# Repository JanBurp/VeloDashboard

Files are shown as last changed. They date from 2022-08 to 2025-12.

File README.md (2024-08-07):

# Velo Dashboard

A bicycle computer made for velomobiles.

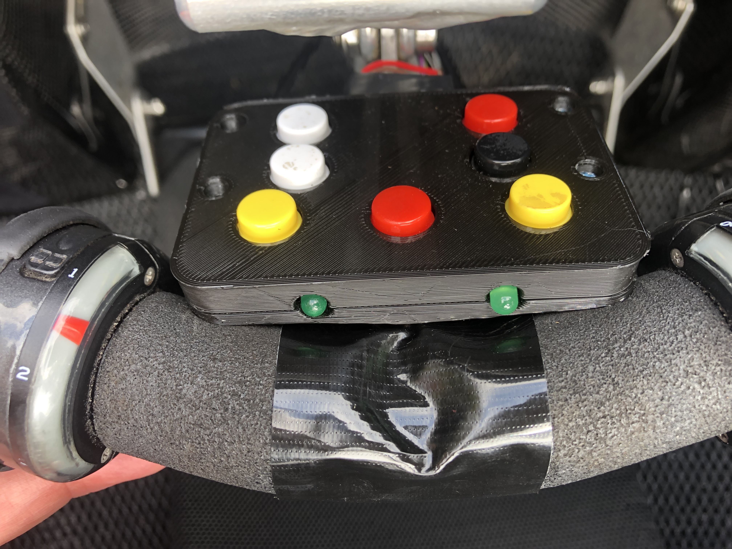
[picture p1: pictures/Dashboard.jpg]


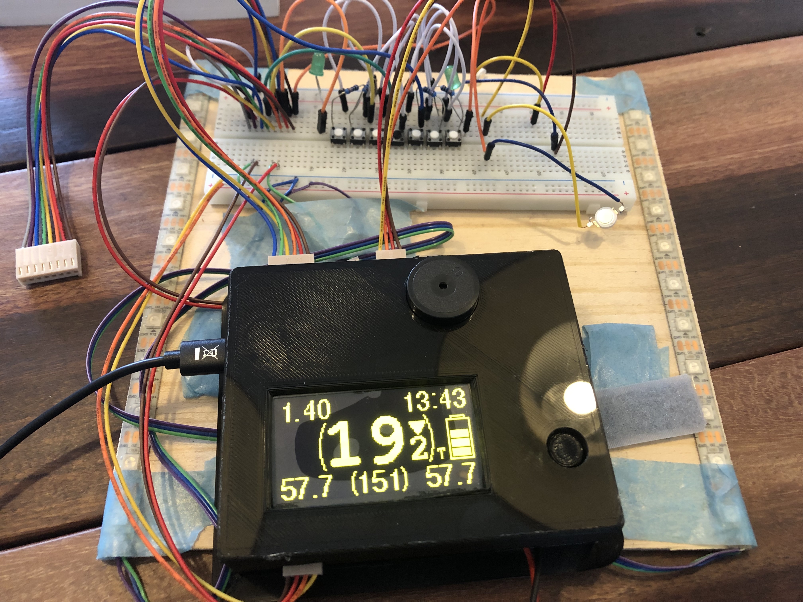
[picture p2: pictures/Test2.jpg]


Walkthrough videos (dutch):
- https://www.youtube.com/watch?v=hqzajXb8Hd0 (inside velomobile)
- https://www.youtube.com/watch?v=B8IcSTC7h3M (test setup)

## Reasons

In the summer of 2022 i bought a second hand [Quest](https://www.velomobiel.nl/quest/) velomobile.
It was in very good shape, had only driven 8000km while only 10 years old, and it fits my budget.

But it was missing blinkers, had a 6V system on board, and two headlights which could be turned on independent from eachother. Which results in my Quest looking cross-eyed :-(
That could be done better.

I also struggled finding the 'perfect' bicycle computer to keep track of at least my current speed, average speed, maximum speed, time, time of the trip, distance, and at least two seperate distance counters.
The most anoying things of these computers are the small screens, the not so ideal combination of functions, button combo's etc. And a GPS one took too long to recognise my location (possibly due to the carbon body).

I took some inspiration found online from other velonauts. Such as:
- [VeloPuter](https://veloputer.wordpress.com/about/)
- [Arduino in VM](https://quest.robbroek.nl/search/label/arduino)
- [Velomobiel Led strip verlichting](https://bickyenzijnfietsen.blogspot.com/2018/10/velomobiel-led-strip-verlichting.html)

## Features

This bicycle computer for a velomibile has these features:

Lighting:
- Drive the normal LED lights that are standard in most velombiles (rear light, brake light, fog light and blinkers if present)
- Drive the (double) head light(s) in several steps (off, dim, normal, beam)
- Drive LED strips on each side of the velomobile. For blinkers (with nice animation!), and normal light for visibility (front, rear and brake lights).

Knobs & Display:
- Big OLED display so i can see it easy.
- All controls are on the steering wheel (with a 3D printed console).
- Knobs for the blinkers, lights and switching through several pages on the display.

Speed & Distance:
- Current speed
- Current average speed
- Current maximum speed
- Distance of current trip
- Total distance of current day
- Distance of previous day
- Average and maximum speed of previous day
- Total distance of the velomobile in total
- Total distance of the velomobile while in my ownership
- At least three different tocal counters wich can be reset independent

Time:
- Current clock time
- Driving time of current trip (excluding stops for traffic lights etc)
- Total time of current trip (including these stops)
- Driving and total time of previous day

Others:
- Current Cadans speed
- Battery status
- Battery saving modes
- Automatic turn off after a set time (to spare battery)
- Option to set the total distance
- Option to set the clock time
- Option to set the wheel circumference
- Optionts to reset all extra counters

# Result

I have a working prototype since december 2022, with several improvements and new featuers since then.

# Manual

## Dashboard



- The yellow buttons are for activating the blinkers. Press and it turns on. Press again to turn off. Press the other and the first one stops and the new one starts. The LED's in front of the dashboard reflects the state of the blinkers.
- The white buttons are for controlling the head and rear lights. And also the lights of the LEDstrips. Press the upper button increases intensity. The lower button decreases intensity. These modes exists: OFF, DIMLIGHT, NORMAL LIGHT, BEAM, FOG.
- The red button on the upper right turns the headlights into BEAM mode while pressed.
- The red button in the middle is not part of the computer: it is it's own circuit and turns of the horn (in my case a Hornitt).
- The black button on the right is for controlling the display on the computer. Pressing cycles to several pages of the display (see below). Long press turns the computer and display into SETUP mode (see below).

## Display modes

Normal pages of the display (cycles through with the blank button):

### Homescreen:
- Speed (big in the center)
- Current distance (topleft)
- Current clock time (topright)
- Average speed (bottomleft)
- Maximun speed (bottomright)
- Cadans / RPM (bottomcenter)
- Icons for headlights and rearligt (middleleft)
- Icons for blinkers and breaklight (topmiddle)
- Icon for battery status (middleright)

### Screen 2 (today):
- Average speed
- Max speed
- Time elapsed while driving (excluding stops)
- Time elapsed from start of driving (including stops)

### Screen 3 (distances):
- Distance of current drive
- Distance of today
- Distance of previous driving day
- Distance of Trip 1

### Screen 3 (totals):
- Total distance of velomobile in my ownershop
- Total distance of velomobile
- Distance of Trip 2
- Distance of Trip 3

## Setup

A long press on the blank button switches to the setup screens. And pressing normal cycles to the setup screens. Long pressing again switches to normal screens. Of the screens there is some help of how to setup the several options.

These are the setup pages:

- Trip - for resetting Trip 1,2 and 3.
- Clock - for setting the time
- Tyre -  for setting the tyre (used for measuring speed and distances). You can select and ERTRO value or in mm.
- Bike - setting the total distance of the bike.

## Others

The computer keeps track of battery status. If the battery is becoming low it will decreases the brightness of the LEDstrips the battery icon on the display starts to blink.

If the battery is very low/almost dead, it will spare itself by turning everything off.

If you forgot to switch the computer off, if will auto power off after three minutes. The last 20 seconds will be shown in the display. If you press a button or start cycling again, the auto-power-off timer will stop.

## Hardware

### Teensy 4.0

The computer is based around a [Teensy 4.0](https://www.pjrc.com/store/teensy40.html). My first attempt was made with a Arduino nano, which is cheaper and uses less power. But i wanted a clock. And the combination of driving LED strips and having an OLED screen was impossible (as far as i know) with te Arduino. The Teensy 4.0 has multiple i2c (OLED) and interrupts. And it also has a build in RTC (Real Time Clock) with power options for a small coin battery to keep the state of the clock. The Teensy has also lots of room for improvements or future additions (SD card storage for example).

### IP67 LEDstrips WS2812B

IP67 means rainproof. And WS2812B means it just has three wires to connect (5V, GND & Data). I have two of them, one for each side of the velomobile. But the computer can also run four of them in case you want four small ones instead of two large ones. I choose the large ones because of easier assembling on my Quest. Downside is it user more power.
Here is a guide for using [WS2812B LEDstrips](https://randomnerdtutorials.com/guide-for-ws2812b-addressable-rgb-led-strip-with-arduino/)

### Power

- For power i choose Lipo batteries of 12.6 Volts. Other batteries are possible.
- [Polo Mini Pushbutton Power Switch](https://www.pololu.com/product/2809) is a on/off switch, whith reverse protection and more.
- Power regulator to 5V. The Teensy has it's own regulator for 5V to 3.3V.

### LED drivers

For driving the front, rear, brake (and maybe blinker) LED's i use [Meanwell LDD Led drivers](https://www.meanwell.com/webapp/product/search.aspx?prod=LDD-L) (LDD-700 for now).

## Schematics

The raw schematics can be found in the [kicad folder](./kicad)

## Software

For developing i used [VScode](https://code.visualstudio.com/) with [PlatformIO](https://platformio.org/). Once setup, i found this much easier for developling compared the Arduino IDE. But thats a software developer speaking ;-)

## 3D print

A STL file for 3D printing the console can be found in the [3D folder](./3d).

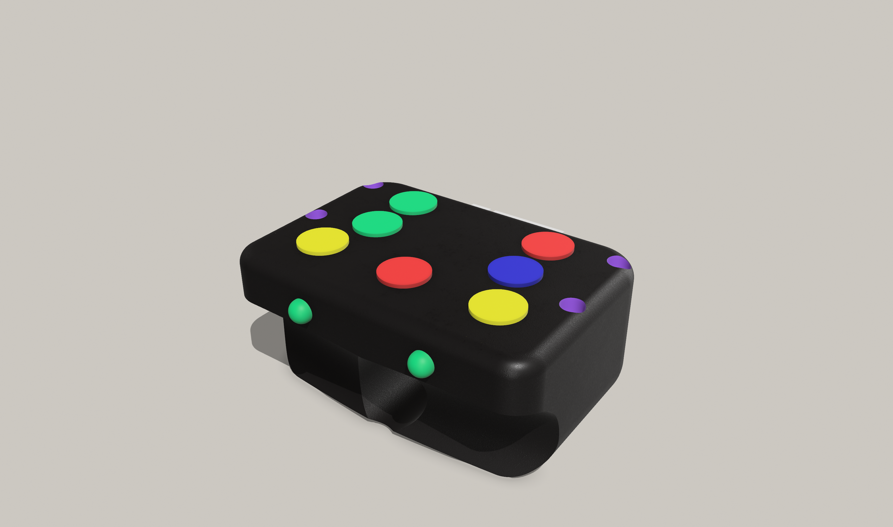
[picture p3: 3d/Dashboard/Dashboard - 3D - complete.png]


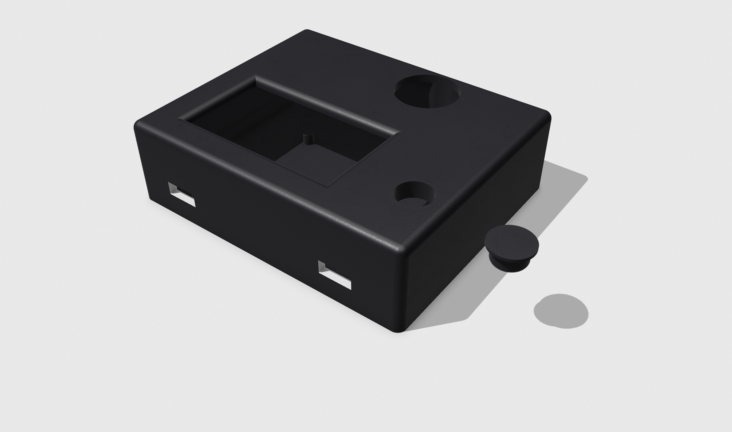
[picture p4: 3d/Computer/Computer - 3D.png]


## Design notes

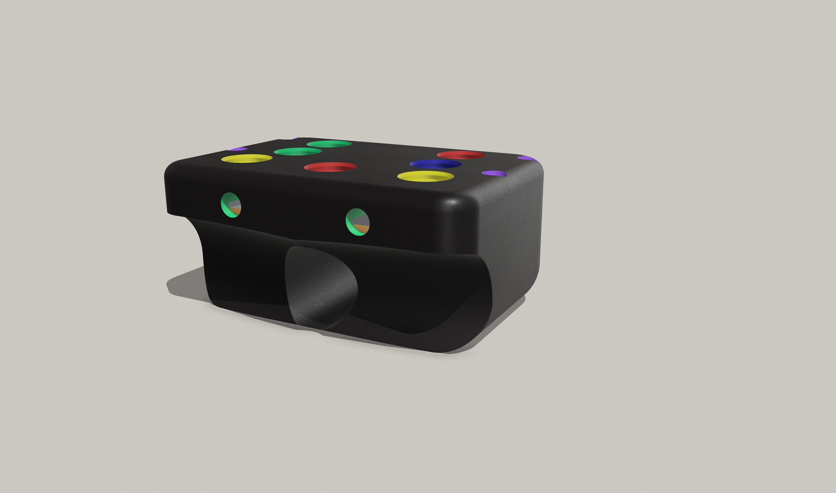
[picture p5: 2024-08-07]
3d/Dashboard/Dashboard_3D.png

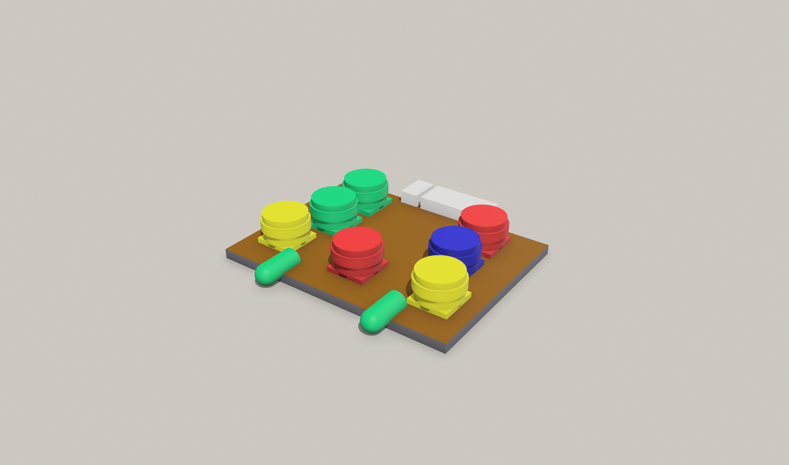
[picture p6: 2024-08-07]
3d/Dashboard/PCB-3D-sketch.png

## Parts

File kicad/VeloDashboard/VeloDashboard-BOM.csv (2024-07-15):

Reference | Value | Datasheet | Footprint | Qty | DNP
BT1 | Battery Cell 3.3V | ~ | Battery:Battery_Panasonic_CR2032-HFN_Horizontal_CircularHoles | 1
C1 | 22µF | ~ | Capacitor_THT:CP_Radial_D10.0mm_P7.50mm | 1
D1 | LEFT | ~ | LED_THT:LED_D5.0mm_Clear | 1
D2 | RIGHT | ~ | LED_THT:LED_D5.0mm_Clear | 1
IC1,IC2,IC3,IC4,IC5,IC6 | LDD-700L | https://datasheet.datasheetarchive.com/originals/distributors/DKDS-14/277848.pdf | LDD:LDD-XXXL | 6
J1 | OLED | ~ | Connector_PinHeader_2.54mm:PinHeader_1x04_P2.54mm_Horizontal | 1
J1.in1 | ~ | ~ | Connector_PinHeader_2.54mm:PinHeader_1x07_P2.54mm_Horizontal | 1
J1.out1 | Polulu Power | ~ | Connector_PinHeader_2.54mm:PinHeader_1x06_P2.54mm_Horizontal | 1
J2 | LED STRIPS | ~ | Connector_PinHeader_2.54mm:PinHeader_1x04_P2.54mm_Horizontal | 1
J3 | To Dashboard | ~ | Connector_PinHeader_2.54mm:PinHeader_1x08_P2.54mm_Horizontal | 1
J4 | To Computer | ~ | Connector_PinHeader_2.54mm:PinHeader_1x08_P2.54mm_Horizontal | 1
J5 | Speed Sensor | ~ | Connector_PinHeader_2.54mm:PinHeader_1x03_P2.54mm_Horizontal | 1
J6 | Headlights | ~ | Connector_PinHeader_2.54mm:PinHeader_1x04_P2.54mm_Horizontal | 1
J7 | Rearlights | ~ | Connector_PinHeader_2.54mm:PinHeader_1x04_P2.54mm_Horizontal | 1
J8 | Blinkers | ~ | Connector_PinHeader_2.54mm:PinHeader_1x04_P2.54mm_Horizontal | 1
J9 | PowerSwitch | ~ | Connector_PinHeader_2.54mm:PinHeader_1x02_P2.54mm_Horizontal | 1
J10 | Addon 1 | ~ | Connector_PinHeader_2.54mm:PinHeader_1x03_P2.54mm_Horizontal | 1
J11 | Addon 2 | ~ | Connector_PinHeader_2.54mm:PinHeader_1x03_P2.54mm_Horizontal | 1
J12 | extra led strips | ~ | Connector_PinHeader_2.54mm:PinHeader_1x04_P2.54mm_Horizontal | 1
R1 | 4M | ~ | Resistor_THT:R_Axial_DIN0207_L6.3mm_D2.5mm_P10.16mm_Horizontal | 1
R2 | 1M | ~ | Resistor_THT:R_Axial_DIN0207_L6.3mm_D2.5mm_P10.16mm_Horizontal | 1
R3,R4,R5,R11,R12,R17,R18 | 100k | ~ | Resistor_THT:R_Axial_DIN0207_L6.3mm_D2.5mm_P10.16mm_Horizontal | 7
R6,R7,R8 | 220k | ~ | Resistor_THT:R_Axial_DIN0207_L6.3mm_D2.5mm_P10.16mm_Horizontal | 3
R9,R10 | 220 | ~ | Resistor_THT:R_Axial_DIN0207_L6.3mm_D2.5mm_P10.16mm_Horizontal | 2
R13,R14,R15,R16,R19,R20 | 47k | ~ | Resistor_THT:R_Axial_DIN0207_L6.3mm_D2.5mm_P10.16mm_Horizontal | 6
R21,R22,R23,R24 | 370 | ~ | Resistor_THT:R_Axial_DIN0207_L6.3mm_D2.5mm_P10.16mm_Horizontal | 4
SW2 | Left | ~ | Button_Switch_THT:SW_PUSH-12mm | 1
SW3 | Down (lights) | ~ | Button_Switch_THT:SW_PUSH-12mm | 1
SW4 | Up (lights) | ~ | Button_Switch_THT:SW_PUSH-12mm | 1
SW5 | Brake | ~ | Button_Switch_THT:SW_PUSH-12mm | 1
SW6 | Horn | ~ | Button_Switch_THT:SW_PUSH-12mm | 1
SW7 | Display | ~ | Button_Switch_THT:SW_PUSH-12mm | 1
SW8 | Right | ~ | Button_Switch_THT:SW_PUSH-12mm | 1
U1 | SN74AHCT125N | http://www.ti.com/general/docs/suppproductinfo.tsp?distId=10 | Package_DIP:DIP-14_W7.62mm_Socket_LongPads | 1
U2 | LC78_05 2.0 | https://www.onsemi.cn/PowerSolutions/document/MC7800-D.PDF | Package_TO_SOT_THT:TO-220-3_Vertical | 1
U3 | Teensy4.0 |  | Teensy:Teensy40_SMT | 1

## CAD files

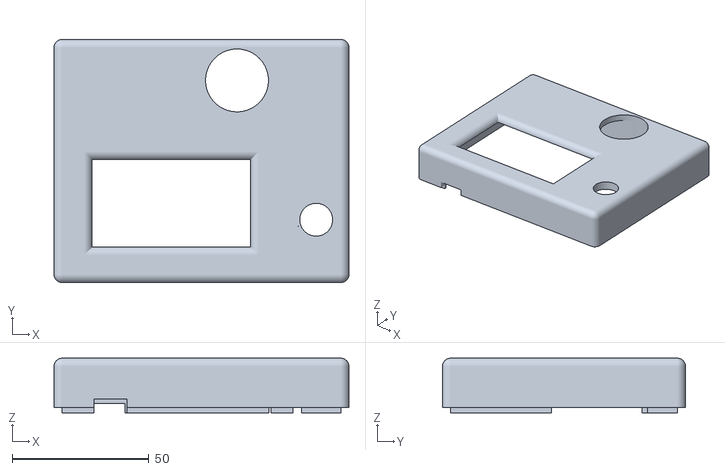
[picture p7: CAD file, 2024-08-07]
3d/Computer/Computer - top.stl
108.0 x 89.0 x 20.0

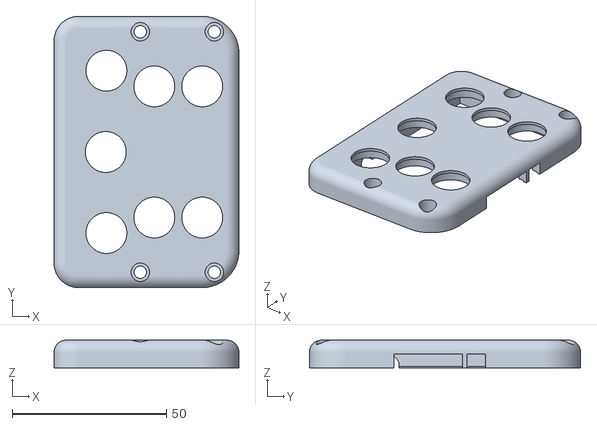
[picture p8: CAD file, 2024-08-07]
3d/Dashboard/VeloDashboard - v3 - top.stl
60.0 x 88.0 x 9.00

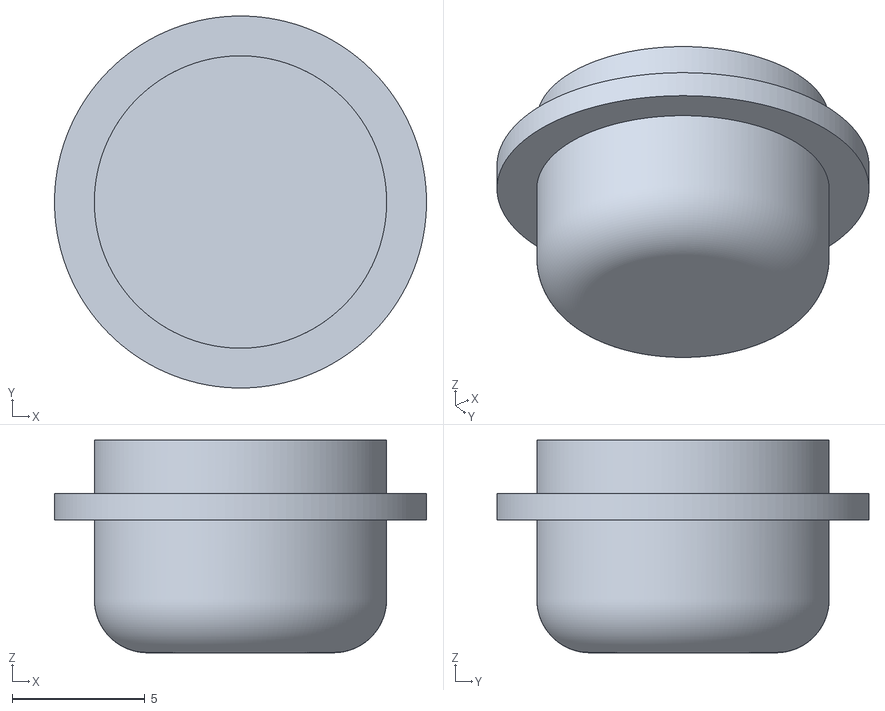
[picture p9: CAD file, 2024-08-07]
3d/Computer/Computer - button.stl
14.0 x 14.0 x 8.00

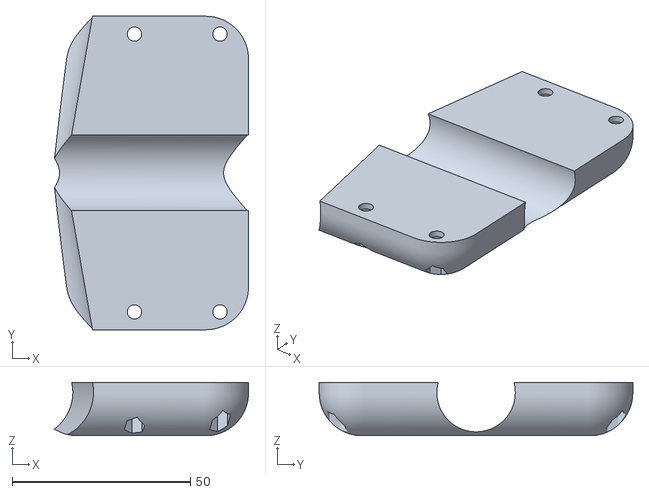
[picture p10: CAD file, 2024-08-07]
3d/Dashboard/VeloDashboard - v3 - bot.stl
54.4 x 88.0 x 15.0

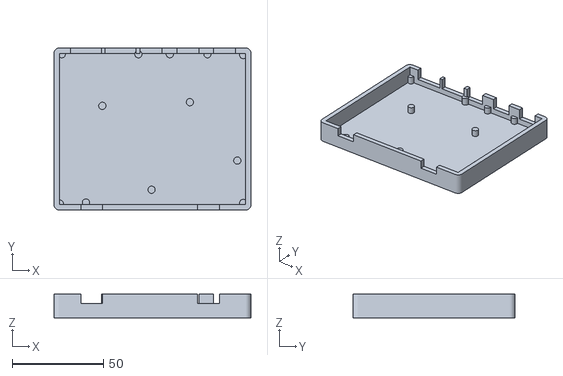
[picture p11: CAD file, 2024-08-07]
3d/Computer/Computer - bot.stl
108.0 x 89.0 x 13.0

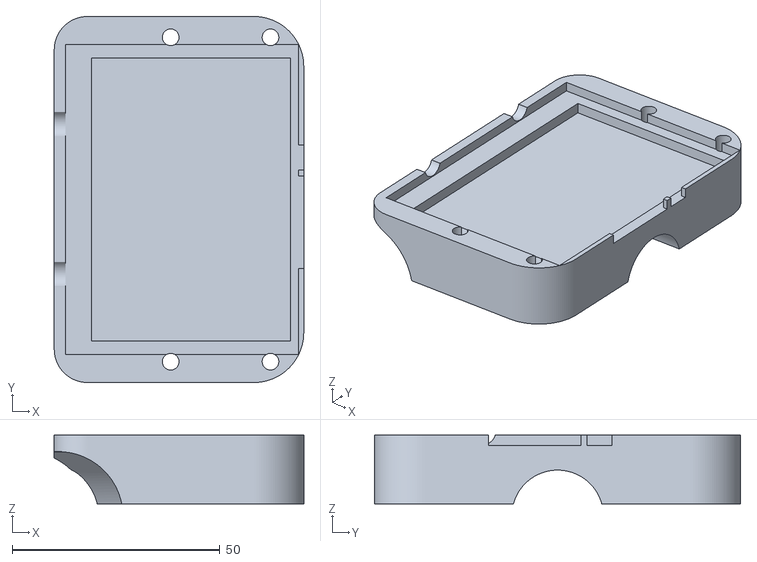
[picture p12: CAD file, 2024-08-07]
3d/Dashboard/VeloDashboard - v3 - mid.stl
60.0 x 88.0 x 16.5

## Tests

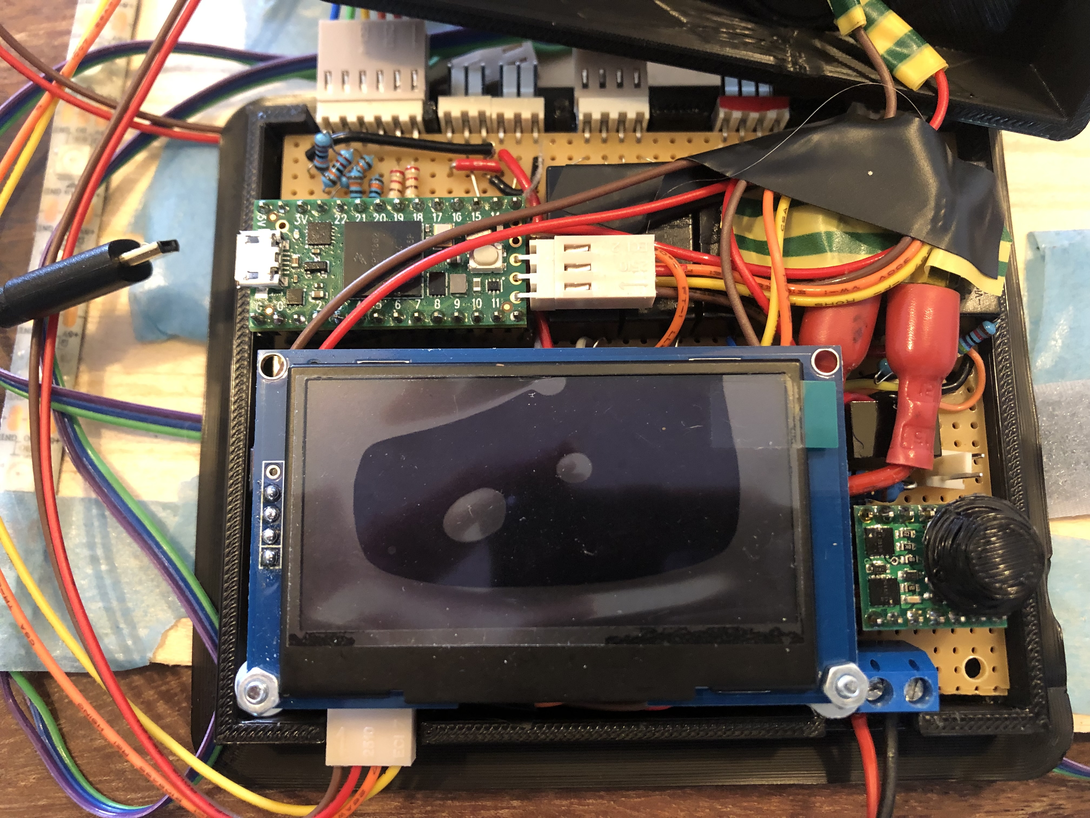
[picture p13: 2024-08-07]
pictures/Test1.jpg

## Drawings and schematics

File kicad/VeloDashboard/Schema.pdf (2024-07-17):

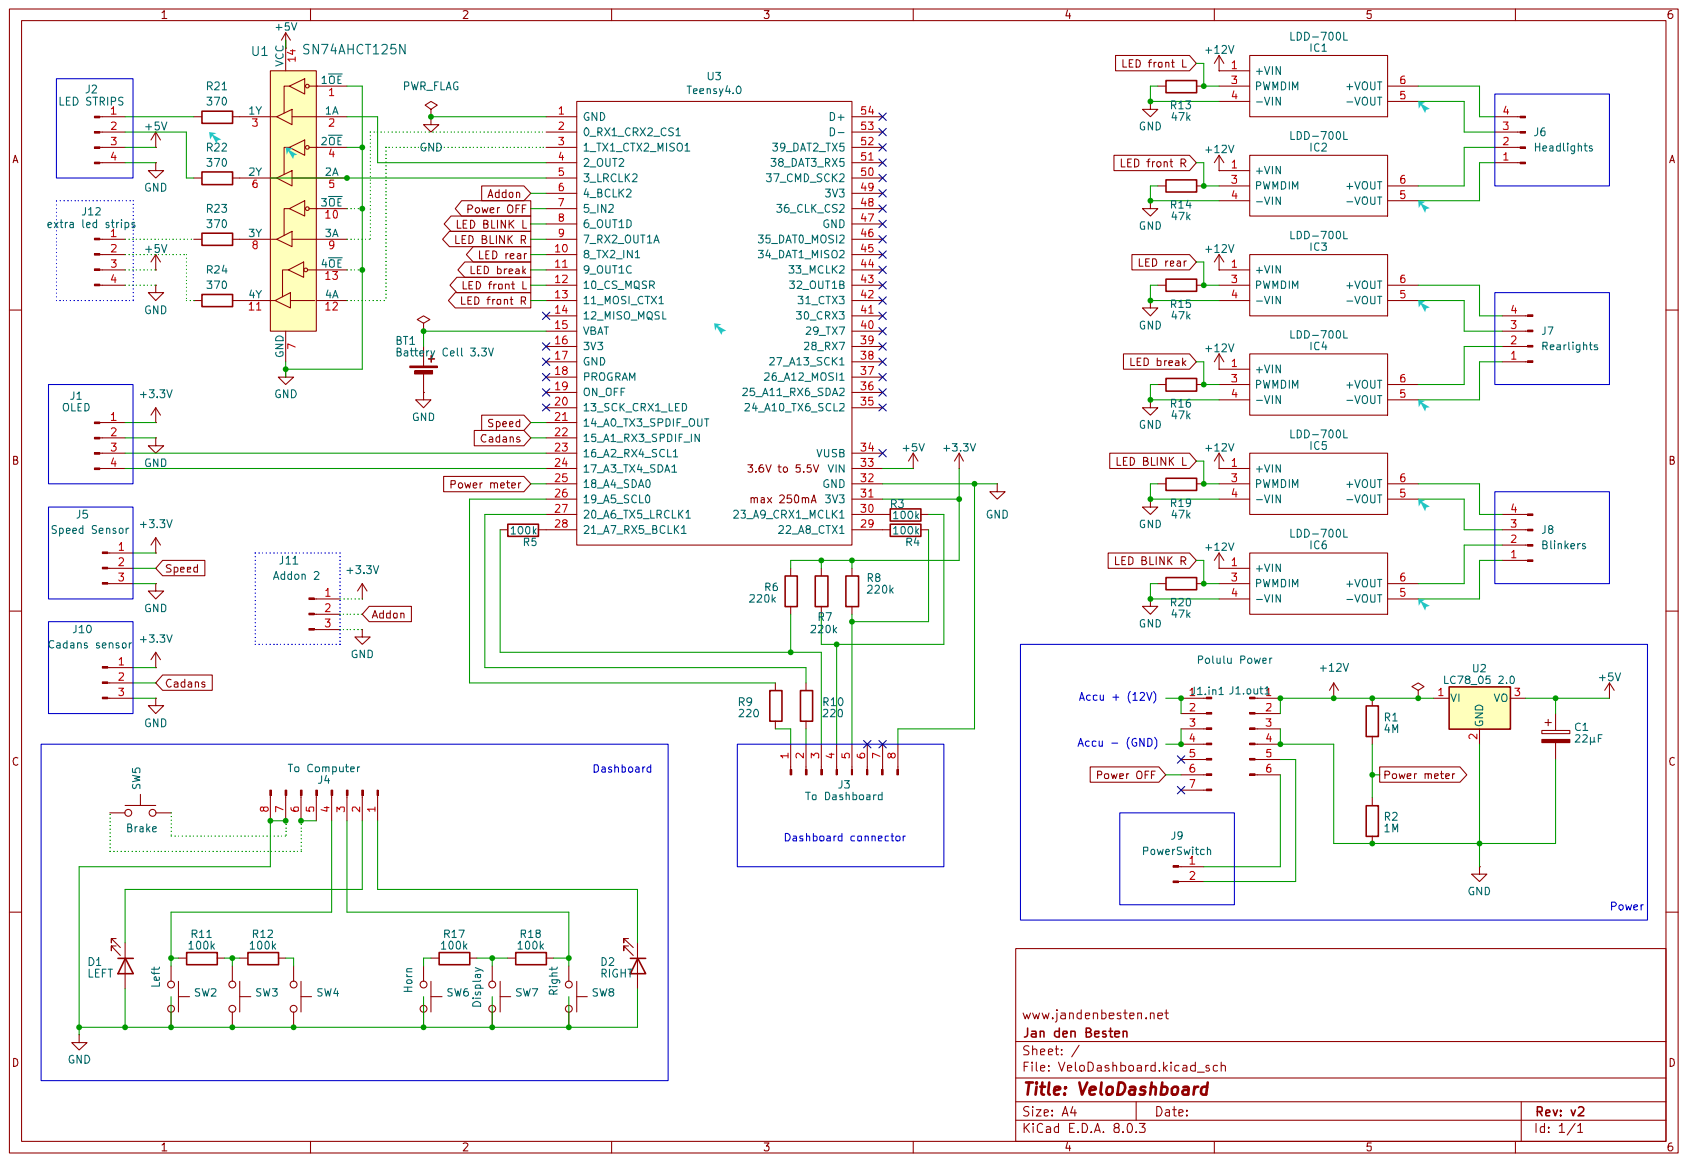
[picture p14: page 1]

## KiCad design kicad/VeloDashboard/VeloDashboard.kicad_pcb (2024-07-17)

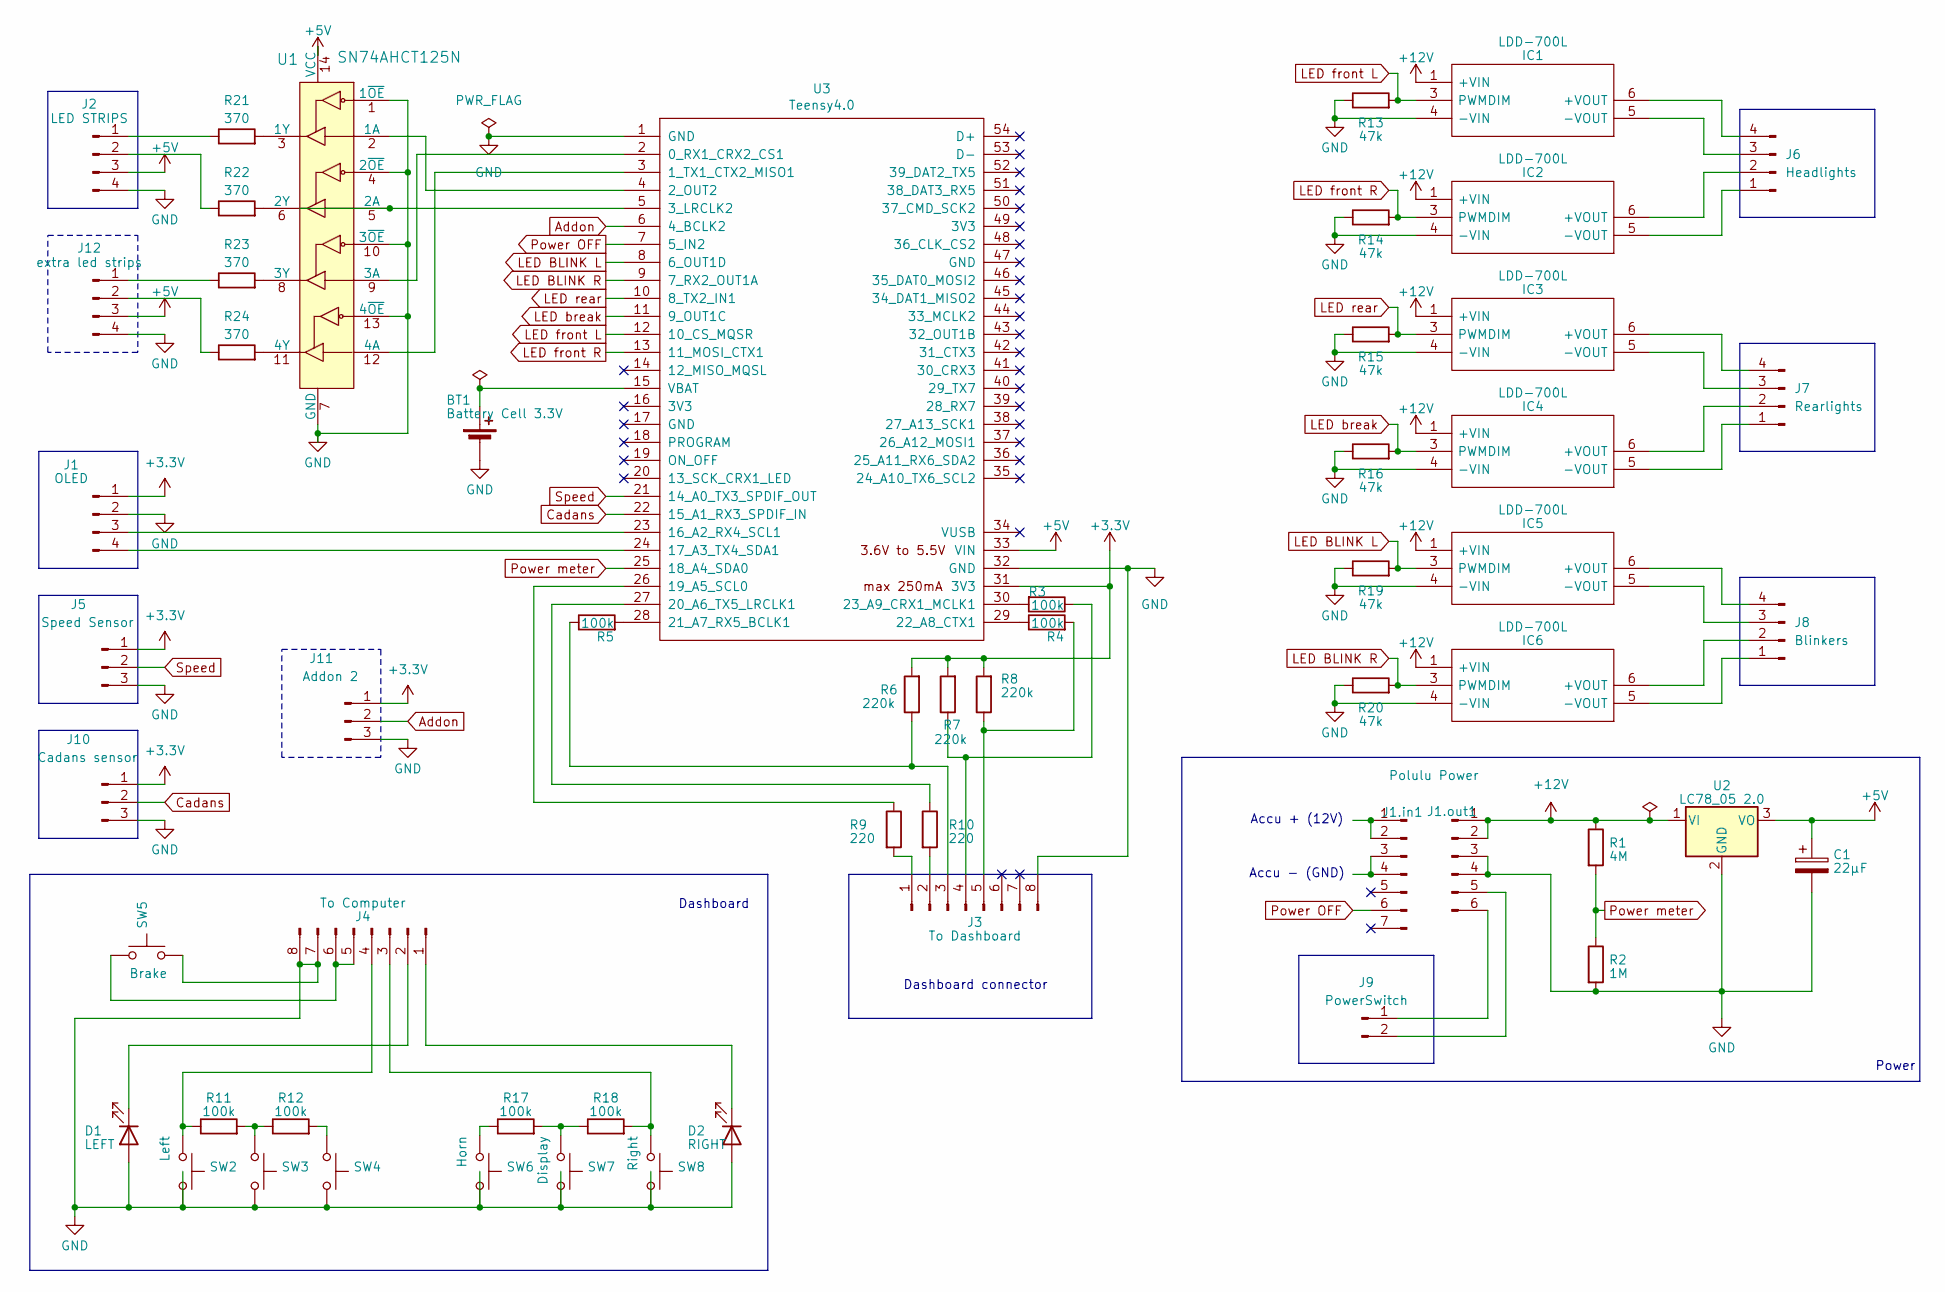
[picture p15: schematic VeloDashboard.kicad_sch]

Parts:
BT1: Battery Cell 3.3V; Battery_Panasonic_CR2032-HFN_Horizontal_CircularHoles
C1: 22µF; CP_Radial_D10.0mm_P7.50mm
D1: LEFT; LED_D5.0mm_Clear
D2: RIGHT; LED_D5.0mm_Clear
IC1, IC2, IC3, IC4, IC5, IC6: LDD-700L; LDD-XXXL; Mouser Part Number 709-LDD-700L
J1: OLED; PinHeader_1x04_P2.54mm_Horizontal
J1.in1: PinHeader_1x07_P2.54mm_Horizontal
J1.out1: Polulu Power; PinHeader_1x06_P2.54mm_Horizontal
J2: LED STRIPS; PinHeader_1x04_P2.54mm_Horizontal
J3: To Dashboard; PinHeader_1x08_P2.54mm_Horizontal
J4: To Computer; PinHeader_1x08_P2.54mm_Horizontal
J5: Speed Sensor; PinHeader_1x03_P2.54mm_Horizontal
J6: Headlights; PinHeader_1x04_P2.54mm_Horizontal
J7: Rearlights; PinHeader_1x04_P2.54mm_Horizontal
J8: Blinkers; PinHeader_1x04_P2.54mm_Horizontal
J9: PowerSwitch; PinHeader_1x02_P2.54mm_Horizontal
J10: Cadans sensor; PinHeader_1x03_P2.54mm_Horizontal
J11: Addon 2; PinHeader_1x03_P2.54mm_Horizontal
J12: extra led strips; PinHeader_1x04_P2.54mm_Horizontal
R1: 4M; R_Axial_DIN0207_L6.3mm_D2.5mm_P10.16mm_Horizontal
R2: 1M; R_Axial_DIN0207_L6.3mm_D2.5mm_P10.16mm_Horizontal
R3, R4, R5, R11, R12, R17, R18: 100k; R_Axial_DIN0207_L6.3mm_D2.5mm_P10.16mm_Horizontal
R6, R7, R8: 220k; R_Axial_DIN0207_L6.3mm_D2.5mm_P10.16mm_Horizontal
R9, R10: 220; R_Axial_DIN0207_L6.3mm_D2.5mm_P10.16mm_Horizontal
R13, R14, R15, R16, R19, R20: 47k; R_Axial_DIN0207_L6.3mm_D2.5mm_P10.16mm_Horizontal
R21, R22, R23, R24: 370; R_Axial_DIN0207_L6.3mm_D2.5mm_P10.16mm_Horizontal
SW2: Left; SW_PUSH-12mm
SW3: Down (lights); SW_PUSH-12mm
SW4: Up (lights); SW_PUSH-12mm
SW5: Brake; SW_PUSH-12mm
SW6: Horn; SW_PUSH-12mm
SW7: Display; SW_PUSH-12mm
SW8: Right; SW_PUSH-12mm
U1: SN74AHCT125N; DIP-14_W7.62mm_Socket_LongPads; MPN SN74AHCT125N; Digi-Key_PN 296-4655-5-ND
U2: LC78_05 2.0; TO-220-3_Vertical
U3: Teensy4.0; Teensy40_SMT

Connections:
+3.3V: J1.1, J5.1, J10.1, J11.1, R6.2, R7.2, R8.2, U3.31 (3V3)
+5V: C1.1, J2.3, J12.3, U1.14 (VCC), U2.3 (VO), U3.33 (VIN)
+12V: IC1.1 (+VIN), IC2.1 (+VIN), IC3.1 (+VIN), IC4.1 (+VIN), IC5.1 (+VIN), IC6.1 (+VIN), J1.out1.1, J1.out1.2, R1.1, U2.1 (VI)
Addon: J11.2, U3.6 (4_BCLK2)
Cadans: J10.2, U3.22 (15_A1_RX3_SPDIF_IN)
GND: BT1.2 (-), C1.2, D1.2 (A), D2.2 (A), IC1.4 (-VIN), IC2.4 (-VIN), IC3.4 (-VIN), IC4.4 (-VIN), IC5.4 (-VIN), IC6.4 (-VIN), J1.2, J1.out1.3, J1.out1.4, J2.4, J3.8, J4.7, J4.8, J5.3, J10.3, J11.3, J12.4, R2.2, R13.1, R14.1, R15.1, R16.1, R19.1, R20.1, SW2.2, SW3.2, SW4.2, SW5.2, SW6.2, SW7.2, SW8.2, U1.1 (1~OE), U1.4 (2~OE), U1.7 (GND), U1.10 (3~OE), U1.13 (4~OE), U2.2 (GND), U3.1 (GND), U3.32 (GND)
LED BLINK L: IC5.3 (PWMDIM), R19.2, U3.8 (6_OUT1D)
LED BLINK R: IC6.3 (PWMDIM), R20.2, U3.9 (7_RX2_OUT1A)
LED break: IC4.3 (PWMDIM), R16.2, U3.11 (9_OUT1C)
LED front L: IC1.3 (PWMDIM), R13.2, U3.12 (10_CS_MQSR)
LED front R: IC2.3 (PWMDIM), R14.2, U3.13 (11_MOSI_CTX1)
LED rear: IC3.3 (PWMDIM), R15.2, U3.10 (8_TX2_IN1)
unnamed: BT1.1 (+), U3.15 (VBAT)
unnamed: D1.1 (K), J4.2
unnamed: D2.1 (K), J4.1
unnamed: IC1.6 (+VOUT), J6.4
unnamed: IC1.5 (-VOUT), J6.3
unnamed: IC2.6 (+VOUT), J6.2
unnamed: IC2.5 (-VOUT), J6.1
unnamed: IC3.6 (+VOUT), J7.4
unnamed: IC3.5 (-VOUT), J7.3
unnamed: IC4.6 (+VOUT), J7.2
unnamed: IC4.5 (-VOUT), J7.1
unnamed: IC5.6 (+VOUT), J8.4
unnamed: IC5.5 (-VOUT), J8.3
unnamed: IC6.6 (+VOUT), J8.2
unnamed: IC6.5 (-VOUT), J8.1
unnamed: J1.3, U3.23 (16_A2_RX4_SCL1)
unnamed: J1.4, U3.24 (17_A3_TX4_SDA1)
unnamed: J1.in1.1, J1.in1.2
unnamed: J1.in1.3, J1.in1.4
unnamed: J1.out1.5, J9.2
unnamed: J1.out1.6, J9.1
unnamed: J2.1, R21.1
unnamed: J2.2, R22.1
unnamed: J3.1, R9.2
unnamed: J3.2, R10.2
unnamed: J3.3, R5.1, R6.1
unnamed: J3.4, R3.1, R7.1
unnamed: J3.5, R4.2, R8.1
unnamed: J4.3, R18.2, SW8.1
unnamed: J4.4, R11.1, SW2.1
unnamed: J4.5, J4.6, SW5.1
unnamed: J12.1, R23.1
unnamed: J12.2, R24.1
unnamed: R11.2, R12.1, SW3.1
unnamed: R12.2, SW4.1
unnamed: R17.1, SW6.1
unnamed: R17.2, R18.1, SW7.1
unnamed: U1.2 (1A), U3.4 (2_OUT2)
unnamed: R21.2, U1.3 (1Y)
unnamed: U1.5 (2A), U3.5 (3_LRCLK2)
unnamed: R22.2, U1.6 (2Y)
unnamed: U1.9 (3A), U3.2 (0_RX1_CRX2_CS1)
unnamed: R23.2, U1.8 (3Y)
unnamed: U1.12 (4A), U3.3 (1_TX1_CTX2_MISO1)
unnamed: R24.2, U1.11 (4Y)
unnamed: R9.1, U3.26 (19_A5_SCL0)
unnamed: R10.1, U3.27 (20_A6_TX5_LRCLK1)
unnamed: R5.2, U3.28 (21_A7_RX5_BCLK1)
unnamed: R4.1, U3.29 (22_A8_CTX1)
unnamed: R3.2, U3.30 (23_A9_CRX1_MCLK1)
Power OFF: J1.in1.6, U3.7 (5_IN2)
Power meter: R1.2, R2.1, U3.25 (18_A4_SDA0)
Speed: J5.2, U3.21 (14_A0_TX3_SPDIF_OUT)

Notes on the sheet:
Accu - (GND)
Dashboard
Power
Accu + (12V)
Dashboard connector

Board: 2 copper layers, 58 parts (0 on the bottom side), 65 nets, no tracks yet.

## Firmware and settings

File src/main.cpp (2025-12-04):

/**
 *
 * VeloDashboard
 *
 *  (c) Jan den Besten
 *
 */

#include "settings.h"

#include <TimeLib.h>
#include "TeensyTimerTool.h"
using namespace TeensyTimerTool;

#include "DashboardClass.h"
#include "BatteryClass.h"
#include "IdleClass.h"
#include "OutputClass.h"
#include "IndicatorClass.h"
#include "LightsClass.h"
#include "SpeedClass.h"
#include "LEDClass.h"
#include "LEDstripClass.h"
#include "DisplayClass.h"

// RTC Time for clock
time_t RTCTime;

// Timers
PeriodicTimer speedCalculationTimer(TCK);

// Inputs & Outputs
DashboardClass Dashboard;
OutputClass Buzzer;

// Classes
DisplayClass Display;
BatteryClass Battery;
IdleClass IdleTimer;
IndicatorClass Indicators;
LightsClass Lights;
SpeedClass Speed;
LEDstripClass LEDstrips;
LedClass LedHeadLightLeft, LedHeadLightRight, LedRearLight, LedBrakeLight, LedBlinkLeft, LedBlinkRight;

/**
 * Get the Teensy3 Time object
 */
time_t getTeensy3Time()
{
    return Teensy3Clock.get();
}

/**
 * Sensor triggers
 */
void speedSensorChange()
{
    Speed.speedTrigger();
    IdleTimer.action();
}

void cadansSensorChange()
{
    Speed.cadansTrigger();
    IdleTimer.action();
}


/**
 * buzzer
 */
void buzzer(bool state)
{
    if (state)
    {
        tone(PIN_BUZZER, BUZZER_TONE);
    }
    else
    {
        noTone(PIN_BUZZER);
    }
}

/*
  Set buzzer on or off
*/
void updateBuzzer()
{
    if (Indicators.isActive())
    {
        buzzer(Indicators.getStateLeft() || Indicators.getStateRight());
    }
    else
    {
        buzzer(false);
    }
}

/**
 * ==== SETUP ====
 */
void setup()
{
    if (DEBUG)
    {
        Serial.begin(115200);
        Serial.println("\n");
        Serial.println("\n");
        Serial.println("TEENSY ALIVE!\n\n");
        Serial.print("F_CPU_ACTUAL = (Mhz)\t");
        Serial.println(F_CPU_ACTUAL / 1000000);
    }

    // Disable unused pins (saves a bit current)
    pinMode(INTERNAL_LED, OUTPUT);
    digitalWrite(INTERNAL_LED, HIGH);
    int unusedPins[] = UNUSED_PINS;
    for (size_t pin = 0; pin < NR_UNUSED_PINS; pin++)
    {
        pinMode(unusedPins[pin], INPUT_DISABLE);
    }

    // Clock
    setSyncProvider(getTeensy3Time);

    // Knobs & Buttons
    Dashboard.init(DASHBOARD_BREAK, DASHBOARD_BUTTONS_LEFT, DASHBOARD_BUTTONS_RIGHT);
    Battery.init(PIN_BATTERY_METER, PIN_POWER_OFF);
    Battery.loop();
    IdleTimer.action();

    Speed.init();

    // Lights & LEDs
    LedHeadLightLeft.init(PIN_HEAD_LIGHT_LEFT);
    LedHeadLightRight.init(PIN_HEAD_LIGHT_RIGHT);
    LedRearLight.init(PIN_REAR_LIGHT);
    LedBrakeLight.init(PIN_BRAKE_LIGHT);
    LedBlinkLeft.init(PIN_BLINK_LEFT);
    LedBlinkRight.init(PIN_BLINK_RIGHT);
    Lights.init(&Battery, &Speed, &LedHeadLightLeft, &LedHeadLightRight, &LedRearLight, &LedBrakeLight);
    Indicators.init(DASHBOARD_LED_LEFT, DASHBOARD_LED_RIGHT, &LedBlinkLeft, &LedBlinkRight, &Speed);
    LEDstrips.init(&Indicators, &Lights, &Battery, &IdleTimer, &Speed);

    // Buzzer
    pinMode(PIN_BUZZER, OUTPUT);
    buzzer(false);

    // Display
    Display.init(&Speed, &Battery, &IdleTimer, &Indicators, &Lights);
    Display.setDisplayMode(DISPLAY_WELCOME);
    Display.show();

    // Startup
    if (!Battery.isDead())
    {
        LEDstrips.startup_animation();
    }

    if (Speed.IsNewDay())
    {
        Speed.startDay();
    }
    else
    {
        if (Speed.IsShortPause())
        {
            Display.askStartupQuestion();
            Display.show();
            Dashboard.waitForButtonPress();
            if (Dashboard.isLightsUp() || Dashboard.isBrake())
            {
                Speed.continueCurrent();
            }
            else
            {
                Speed.resetCurrent();
            }
        }
        else
        {
            Speed.resetCurrent();
        }
    }

    Display.setDisplayMode(DISPLAY_MINIMAL);
    Display.show();
    digitalWrite(INTERNAL_LED, LOW);

    pinMode(PIN_SPEED, INPUT_PULLUP);
    attachInterrupt(digitalPinToInterrupt(PIN_SPEED), speedSensorChange, CHANGE);

    pinMode(PIN_CADANS, INPUT_PULLUP);
    attachInterrupt(digitalPinToInterrupt(PIN_CADANS), cadansSensorChange, CHANGE);

    speedCalculationTimer.begin([] { Speed.loop(); }, SPEED_CALCULATION_TIMER);
}

/*
  Read Dashboard buttons
*/
void readButtons()
{
    // Break & Beam
    Lights.setBrake(Dashboard.isBrake());
    Lights.setBeam(Dashboard.isBeam());

    // Others
    if (Dashboard.read())
    {
        IdleTimer.action();

        // LEFT - RIGHT
        if (Display.isSettingsMenu())
        {
            if (Dashboard.isIndicatorLeft())
            {
                Display.moveCursor(1);
            }
            if (Dashboard.isIndicatorRight())
            {
                Display.moveCursor(-1);
            }
        }
        else
        {
            if (Dashboard.isIndicatorLeft())
            {
                Indicators.setLeft();
            }
            if (Dashboard.isIndicatorRight())
            {
                Indicators.setRight();
            }
        }

        // UP - DOWN
        if (Display.isResetTripMenu())
        {
            if (Dashboard.isLightsUp())
            {
                Speed.resetTripDistance(1);
            }
            if (Dashboard.isLightsDown())
            {
                Speed.resetTripDistance(2);
            }
            if (Dashboard.isIndicatorLeft())
            {
                Speed.resetTripDistance(3);
            }
        }
        else if (Display.isSetClockMenu())
        {
            if (Dashboard.isLightsUp())
            {
                Speed.increaseClock(Display.cursorAmount());
            }
            if (Dashboard.isLightsDown())
            {
                Speed.decreaseClock(Display.cursorAmount());
            }
        }
        else if (Display.isSetTyreMenu())
        {
            if (Dashboard.isLightsUp())
            {
                Speed.increaseCircumference(Display.cursorAmount());
            }
            if (Dashboard.isLightsDown())
            {
                Speed.decreaseCircumference(Display.cursorAmount());
            }
        }
        else if (Display.isSetTotalMenu())
        {
            if (Dashboard.isLightsUp())
            {
                Speed.increaseTotal(Display.cursorAmount());
            }
            if (Dashboard.isLightsDown())
            {
                Speed.decreaseTotal(Display.cursorAmount());
            }
        }
        else
        {
            if (Dashboard.isLightsUp())
            {
                Display.setDisplayModeHome();
                Lights.increaseLights();
                if (Dashboard.isLongPressed())
                {
                    Lights.setFogLight();
                }
            }
            if (Dashboard.isLightsDown())
            {
                Display.setDisplayModeHome();
                Lights.decreaseLights();
                if (Dashboard.isLongPressed())
                {
                    Lights.resetLights();
                }
            }
        }

        // Display pages
        if (Dashboard.isDisplay())
        {
            Display.nextDisplayMode();
        }
        if (Dashboard.isDisplay() && Dashboard.isLongPressed())
        {
            Display.toggleSettings();
        }
    }

    if (IdleTimer.warning())
    {
        Display.setDisplayModeHome();
        Lights.resetLights();
    }
}


/*

  ==== LOOP ====

*/
void loop()
{
    readButtons();
    updateBuzzer();

    if (IdleTimer.ended())
    {
        Speed.storeMemory();
        LEDstrips.off();
        Lights.off();
        Display.off();
        Battery.powerOff();
    }

    if (Battery.isDead())
    {
        LEDstrips.off();
        Lights.off();
        Display.off();
        if (Battery.delayedPowerOff())
        {
            Speed.storeMemory();
            Battery.powerOff();
        }
    }
    else
    {
        LEDstrips.loop();
        Lights.loop();
        Display.show();
    }

    if (!Dashboard.isBrake())
    {
        Battery.loop();
    }
}

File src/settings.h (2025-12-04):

#pragma once

#define DEBUG false // [default = false] - set to true for Serial output
#define TEST false // [default = false] - set to true for local test environment

/*
  WHEELS
*/

typedef struct
{
    char name[8];
    float circumference;
} Wheel;

// https://www.cateyeamerica.com/tire-size-calculator/
#define NR_ETRTO_WHEELS 13
Wheel Wheels[NR_ETRTO_WHEELS] = {
    {"23-406", 1.418},
    {"25-406", 1.431},
    {"26-406", 1.437},
    {"28-406", 1.450},
    {"30-406", 1.462},
    {"32-406", 1.475}, // CCU 32
    {"35-406", 1.494}, // Schwalbe Marathon+
    {"38-406", 1.512},
    {"40-406", 1.525},
    {"42-406", 1.538}, // CCU 42
    {"44-406", 1.550},
    {"50-406", 1.588},
    {"56-406", 1.625},
};


#if TEST
    #define BIKE_LENGTH 15 // cm
#else
    #define BIKE_LENGTH 285 // cm
#endif


#define BIKE_DISTANCE_START 8060
#define MAX_TIME_SHORT_BRAKE 21600 // 6 hours = 60*60*6 seconds

// total bytes = 4 * 20 = 80 bytes
typedef struct
{
    unsigned long timestamp; // Time when data is stored

    unsigned long totalDistance; // ODO (meters)
    float tripDistance1; // sub total 1..3
    float tripDistance2;
    float tripDistance3;

    float currentDistance; // current trip
    unsigned long currentStartTime;
    unsigned long currentTime;
    float currentAverageSpeed;
    float currentMaxSpeed;

    float dayDistance; // day totals
    unsigned long dayStartTime;
    unsigned long dayTime;
    float dayAverageSpeed;
    float dayMaxSpeed;

    float prevDistance; // prev day
    unsigned long prevTime;
    float prevAverageSpeed;
    float prevMaxSpeed;

    float wheelCircumference; // config
} MemoryStruct;


/*
    LED light intensities
*/

#define HEAD_LED_OFF_INTENSITY 0
#define HEAD_LED_DIM_INTENSITY 0
#define HEAD_LED_ON_INTENSITY 4 // 4 = minimum light
#define HEAD_LED_NORMAL_INTENSITY 92
#define HEAD_LED_BEAM_INTENSITY 140 // 140 = maximum light
#define HEAD_LED_FOG_INTENSITY 140

#define REAR_LED_OFF_INTENSITY 0
#define REAR_LED_DIM_INTENSITY 4
#define REAR_LED_ON_INTENSITY 16
#define REAR_LED_NORMAL_INTENSITY 32
#define REAR_LED_BEAM_INTENSITY 64
#define REAR_LED_FOG_INTENSITY 140 // 140 = max

#define BLINK_OFF 0
#define BLINK_ON 140

#define BRAKE_LEDS_OFF 0
#define BRAKE_LEDS_FOG 64
#define BRAKE_LEDS_ON 140


/*
    TIMERS
*/
#define INDICATOR_TIMER 350ms
#define INDICATOR_TIMER_INT 350
#define INDICATOR_TIMER_STEP 35ms
#define ALARM_TIMER 350ms
#if TEST
    #define WELCOME_ANIMATION 250
#else
    #define WELCOME_ANIMATION 50
#endif

#if TEST
    #define IDLE_TIMER 120
    #define IDLE_WARNING_TIMER 20
#else
    #define IDLE_TIMER 180 // seconds
    #define IDLE_WARNING_TIMER 30 // seconds
#endif
#define SPEED_CALCULATION_TIMER 1000ms
#define SPEED_CALCULATION_TIME 1000
#define MINUTE 60000
#define BUZZER_TONE 440

/*
    DISPLAY
*/
#define SCREEN_WIDTH 128
#define SCREEN_HEIGHT 64
#define SCREEN_THIRD_HEIGHT 21
#define SCREEN_HALF_HEIGHT 32
#define SCREEN_HALF_WIDTH 64
#define SCREEN_HALF_HEIGHT_INFO 40
#define SCREEN_HALF_HEIGHT_VALUES 50

/*
  DISPLAY MODES
 */
#define DISPLAY_WELCOME 0
#define DISPLAY_MINIMAL 1
#define DISPLAY_HOME 2
#define DISPLAY_CURRENT 3
#define DISPLAY_TODAY 4
#define DISPLAY_PREV 5
#define DISPLAY_TOTALS 6

#define DISPLAY_SETTINGS_TRIP 10
#define DISPLAY_SETTINGS_CLOCK 11
#define DISPLAY_SETTINGS_TYRE 12
#define DISPLAY_SETTINGS_TOTAL 13

/*
  LED STRIPS
*/

#define WELCOME_LENGTH 1

#define BRIGHTNESS 255
#define FRAMES_PER_SECOND 100
#if TEST
    #define NUM_LEDS 12
    #define NUM_LIGHT_LEDS_FRONT 5
    #define NUM_LIGHT_LEDS_BACK 5
    #define NUM_INDICATOR_LEDS 5
    #define NUM_SPEED_LEDS 1
    #define MAX_MILLIAMPS 400
#else
    #define NUM_LEDS 169 // 2,85 m * 66 = 188
    #define NUM_LIGHT_LEDS_FRONT 36
    #define NUM_LIGHT_LEDS_BACK 48
    #define NUM_INDICATOR_LEDS 70
    #define NUM_SPEED_LEDS 3
    #define MAX_MILLIAMPS 2000
#endif

#define LEFT -1
#define BOTH 0
#define RIGHT 1

/*
  Speed
*/

#define SENSOR_BUFF 25
// #define MIN_SENSOR_TIME 75 // ~ 72 km/h
#define MIN_SENSOR_TIME 50 // ~ 100 km/h
#define MAX_SENSOR_TIME 3000
#define MIN_SPEED 2


/*
 * PINS (south L->R)
 */

// 0 - unused -> extra LEDstrips
// 1 - unused -> extra LEDstrips
#define PIN_LEFT_STRIP 2
#define PIN_RIGHT_STRIP 3
// 4 - unused -> addon
#define PIN_POWER_OFF 5
#define PIN_BLINK_LEFT 6
#define PIN_BLINK_RIGHT 7
#define PIN_REAR_LIGHT 8
#define PIN_BRAKE_LIGHT 9
#define PIN_HEAD_LIGHT_LEFT 10
#define PIN_HEAD_LIGHT_RIGHT 11
#define PIN_BUZZER 12

/*
 * PINS (north L-R)
 */
#define DASHBOARD_BREAK 23
#define DASHBOARD_BUTTONS_LEFT 22
#define DASHBOARD_BUTTONS_RIGHT 21
#define DASHBOARD_LED_RIGHT 19
#define DASHBOARD_LED_LEFT 20
#define PIN_BATTERY_METER 18
// 17 - DISPLAY SCL
// 16 - DISPLAY SDA
#define PIN_CADANS 15 // 15 - unused
#define PIN_SPEED 14
#define INTERNAL_LED 13 // 13 - unused - OFF

/**
 * Unused PINS
 */
#define UNUSED_PINS {0, 1, 4, 15, 16, 17}
#define NR_UNUSED_PINS 6

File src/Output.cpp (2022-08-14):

#ifndef Output_h
#define Output_h

#include "Arduino.h"

class Output {

	public:

		/**
		 * Setup the OUTPUT, specifying and optional minimum "on" duration for user visibility
		 */
		void init(byte pin, unsigned int minDurationMs = 50) {

			this->pin = pin;
			this->minDurationMs = minDurationMs;

			this->state = false;
			this->stateHardware = false;
			this->blinkMs = 0;
			this->lastOnMs = 0;

			pinMode(this->pin, OUTPUT);
			digitalWrite(this->pin, LOW);

		}

		/**
		 * Turn the OUTPUT on or off.
		 * If a minimum duration was set, it could not turn off if it was
		 * on for too little, you need to call loop() to update the state.
		 */
		void set(bool state) {

			this->blinkMs = 0; // Stop blinking
			this->state = state;

			if (state) {

				// Remember last time it was requested to be on
				this->lastOnMs = millis();

				// Turn on the OUTPUT if necessary
				if (!this->stateHardware) {
					this->stateHardware = true;
					digitalWrite(this->pin, HIGH);
				}

			} else {

				// Turn the OUTPUT off if necessary
				this->loop();

			}

		}

		/**
		 * Starts blinking with given period, until any other method is called.
		 * Use duty to specify how long the OUTPUT will be on, and invert to flip the blinking phase.
		 * This method can also be used make it fade, using a short period and duty to adjust brightness.
		 * Make sure to call loop() to keep the OUTPUT blinking.
		 */
		void blink(unsigned int periodMs = 500, float duty = 0.5, bool invert = false) {
			this->blinkMs = periodMs;
			this->blinkDuty = max(0, min(1, duty));
			this->blinkStartedMs = millis() - (invert ? duty * periodMs : 0);
		}

		/**
		 * Turn the OUTPUT off if necessary, or keep it blinking.
		 * Call this in the main loop.
		 */
		void loop() {

			if (this->blinkMs > 0) {

				unsigned long t = ((millis() - this->blinkStartedMs) % this->blinkMs);
				this->stateHardware = t < (this->blinkMs * this->blinkDuty);
				digitalWrite(this->pin, this->stateHardware);

			} else {

				// Turn the OUTPUT off if necessary
				if (!this->state && this->stateHardware) {
					if (millis() - this->lastOnMs >= this->minDurationMs) {
						this->stateHardware = false;
						digitalWrite(this->pin, LOW);
					}
				}

			}

		}

		void on() {
			this->set(true);
		}

		void off() {
			this->set(false);
		}

		void toggle() {
			this->set(!state);
		}

        bool getState() {
            return this->stateHardware;
        }

		/**
		 * Turn on the OUTPUT, then turn it off immediately.
		 * A single impulse of light will be visible if OUTPUT's minDurationMs is long enough.
		 */
		void flash() {
			this->set(true);
			this->set(false);
		}

	private:
		byte pin;
		unsigned int minDurationMs;
		bool state;
		bool stateHardware;
		unsigned int blinkMs;
		unsigned long blinkStartedMs;
		float blinkDuty;
		unsigned long lastOnMs;

};

#endif

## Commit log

2022-08-14 Working with simple LED’s
2022-08-15 LEDstrips added
2022-08-20 Speed sensor & Display
2022-08-27 Working on Teensy
2022-08-27 LED strips working
2022-08-29 Longer Ledstrip & color finetuning
2022-09-21 Hardware pins changed (after soldering)
2022-09-21 Indicator switch (and UI button changed)
2022-09-21 RTC clock & battery
2022-09-21 Extra button functions
2022-09-22 Finetune LEDS after installing
2022-09-23 bug: when changing indicators fast, no reset was done
    [main.cpp]
2022-09-25 sensor analog read
2022-09-25 bug solved & use of trigger
    [main.cpp]
2022-10-02 simple power calculation
2022-10-09 Small adjustment to LED’s
2022-10-14 TEST number of LED’s and max current/brightness set
2022-10-16 other timers (pt1)
2022-10-16 Using Teensy Timers
2022-10-23 Wheels in settings
2022-10-23 battery indicator
2022-10-23 Icons for Battery & Lights - Knobs for Lights
2022-11-13 LEDstrip usages indicator
2022-11-19 Battery Management
2022-11-21 finetuning battery
2022-11-25 PowerOff (after 60sec dead battery)
2022-12-24 5 buttons dahsboard
2022-12-27 Revert "Merge branch 'feature_3_battery' into develop"
    This reverts commit 6dc1b7cbc0be2a0b24a8220ec47080c7c38e3227, reversing
    changes made to c509d7db925ed054896ee03a1eab9e0b950f60f2.
    [BatteryClass.h]
2022-12-27 Battery Test
2022-12-27 Idle Timer & Pause Display
2023-01-02 New Dashboard
    - Better spread of buttons
    - No SHIFT button
    - Detection of LongPress
2023-01-03 Changes to Battery life measurement
2023-01-06 UI: Indicator control: easy switch
2023-01-08 Builtin LED off
2023-01-08 Teensy LED off (did not work)
    [main.cpp, settings.h]
2023-01-08 Idle timer LEDstrips countdown animation
2023-01-08 Idle Timer warning shorter (30 secs)
    [settings.h]
2023-01-08 Adding lost km’s to ODO
2023-01-08 Some indicator animation bugs solved (timers…)
    [LEDstripClass.h, main.cpp]
2023-01-13 Indicator switch reageert nu meteen
2023-01-13 bug: als je meteen van de ene naar de andere richtingaanwijzer ging bleef strip zwart
    [LEDstripClass.h]
2023-01-13 Battery finetuning
2023-01-14 Display sensor only on HOME
2023-02-05 Speed bugs (dayDist, tripTime, avg)
    [SpeedClass.h]
2023-02-05 bug: Speed not started
    [SpeedClass.h]
2023-02-10 added more wheel circumferences (standards)
2023-02-13 Setting tyre circumference (some refacturing menu)
2023-02-17 first step for pcb
    [VeloDashboard.kicad_pcb, VeloDashboard.kicad_sch, VeloDashboard.sch]
2023-02-25 Teensy & LDD & Led strips
    [VeloDashboard.kicad_sch]
2023-02-27 Power & Dashboard & OLED & others
    [VeloDashboard.kicad_sch]
2023-03-06 buzzer with mosfet added
    [VeloDashboard.kicad_sch]
2023-04-09 pcb more
2023-04-09 bug: display settings should not be commented
    [settings.h]
2023-07-01 tighter dashboard buttons
2023-07-01 Better Battery Measurement (due to horn)
2023-07-01 Toeter & Relay toegevoegd
    [VeloDashboard.kicad_sch]
2023-07-01 Cleaner debug battery
2023-07-08 bug: on startup battery was dead
    [BatteryClass.h]
2023-07-24 Better power meter
2023-07-24 busy with redesign display
    [DisplayClass.h, settings.h]
2023-07-25 swap time & distance
    [DisplayClass.h]
2023-07-25 swap clock & distance back
    [DisplayClass.h]
2023-08-08 Adjust battery level
    [LiPo.xlsx]
2023-08-09 bug: When keeping day distance, time & avg where calculated wrong
    [SpeedClass.h, settings.h]
2023-08-27 Battery meter change
    [LiPo.xlsx]
2023-09-02 Longer battery measurement
2023-09-04 only ask startup if current distance > 100m
2023-09-04 Aks only when distance longer & brake is shor (within 6 hours)
2023-09-11 bug: current / day
    [SpeedClass.h, main.cpp]
2023-09-11 Teensy Clock speed
2023-09-12 slow cpu doesn’nt work
2023-09-12 CPU speed 80Mhz (48 gives LEDstrip problems)
2023-09-12 LEDstrips OFF (BLACK) when dimmed
2023-09-12 Shorter indicator LEDstrip Length
    [LEDstripClass.h]
2023-09-16 bug in adding to totalDistance
    [SpeedClass.h, settings.h]
2023-09-22 Lights finetuning (for power restrictions)
2023-10-05 BUG: startDay when should be resetCurrent
    [main.cpp]
2023-10-05 swap speeds and today on display pages
    [settings.h]
2023-10-05 Longer battery measurment
2023-10-25 turn off LEDstrip brake lights when paused
2023-10-29 Brakelight savind (off when paused)
2023-11-17 no battery checking when brake is on - longer battery timing
2023-11-18 Battery Brake fineuning
2023-12-22 Indicartor LEDS on dashboard (utp)
2023-12-23 Brake LED
2023-12-23 updatet schematics
    [VeloDashboard.kicad_sch, untitled.kicad_sch]
2024-02-16 filter out strange doubling of (max)speed
2024-02-16 dimmed is flickering to much…
2024-02-16 moved to docs
    [LiPo.xlsx]
2024-02-16 moved kicad project
    [VeloDashboard.kicad_pcb, VeloDashboard.kicad_sch, VeloDashboard.sch]
2024-02-17 added 3d design
    [VeloDashboard - Bottom.stl, VeloDashboard - Top.stl]
2024-07-12 pcb cleanup
    [VeloDashboard.kicad_pcb, VeloDashboard.kicad_sch]
2024-07-12 Added brakelights
2024-07-13 dahsboard refacture
    [VeloDashboard.kicad_sch]
2024-07-13 Battery button same R
2024-07-13 Refacture schema
    [VeloDashboard.kicad_sch]
2024-07-13 update pcb
    [VeloDashboard.kicad_sch]
2024-07-13 added blinker drivers
    [VeloDashboard.kicad_sch]
2024-07-14 update to kicad 8
    [VeloDashboard.kicad_sch]
2024-07-14 raw pcb
    [VeloDashboard.kicad_pcb]
2024-07-14 rule check
    [VeloDashboard.kicad_sch]
2024-07-15 Refacture schematic & raw pcb
    [VeloDashboard.kicad_pcb, VeloDashboard.kicad_sch]
2024-07-15 Refacture voor uitbreidingen
    [VeloDashboard.kicad_sch]
2024-07-15 BOM added
    [VeloDashboard-BOM.csv, VeloDashboard.kicad_pcb]
2024-07-15 rewire dashboard connectors
    [VeloDashboard.kicad_sch]
2024-07-17 refacture due to soldering
    [VeloDashboard.kicad_pcb, VeloDashboard.kicad_sch]
2024-07-23 power adjustments
    [VeloDashboard.kicad_sch]
2024-07-23 Buttons shuffle
2024-07-24 update dasbboard connector on computer
    [VeloDashboard.kicad_sch]
2024-07-24 Teensy internal LED on
2024-07-25 BUG: dashboard buttons threshold
    [settings.h]
2024-07-25 BUG: totaltime counted wrong
    [SpeedClass.h, settings.h]
2024-07-25 hack to make high resistors work
2024-07-25 Don’t ask distance when TEST
2024-08-03 Indicatord back on display & shorter welcome
    [DisplayClass.h, settings.h]
2024-08-03 Teensy internal LED off after power up animation
2024-08-04 added buzzer (hardware)
    [VeloDashboard.kicad_sch]
2024-08-06 battery management: LEDstrips off when low
2024-08-06 3D designs updated
    [Computer - bot.stl, Computer - button.stl, Computer - top.stl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]
2024-08-07 bug: LEDstrips off when battery low
    [LEDstripClass.h, main.cpp]
2024-08-07 3D improvements
    [Computer - button.stl, Computer - top.stl]
2024-08-10 rearlight animation removed & dimming LEDstrips with lower battery
2024-08-10 bug: font for clock too big
    [DisplayClass.h]
2024-08-16 bugs: calculating day totals & prev totals
    [BatteryClass.h, SpeedClass.h, settings.h]
2024-08-16 bug: vertical shift OLED
    [DisplayClass.h]
2024-08-17 smalle improvements & minor bugs
    [DisplayClass.h, SpeedClass.h, settings.h]
2025-09-21 better? speed filter
2025-09-21 Minder voorLED’s aan
2025-09-21 Timer for minimal display
2025-09-26 less filtereing of speed
2025-10-19 Better speedtrigger filtering?
